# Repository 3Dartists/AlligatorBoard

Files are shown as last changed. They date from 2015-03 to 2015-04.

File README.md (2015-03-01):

Alligator Board
===============

The New Generation Electronic for RepRap 3D printer

The Alligator Board is designed to be a complete and reliable solution as RepRap 3D printer 
electronic control board. The base module features everything you need to build a standard 3D printer, 
and with the expansion piggy this is the most complete solution for complex 3D printer.

It is based on the 32 bit Cortex M3 ATSAM3X8EA-AU microcontroller (Arduino Due CPU)
This represents a big step forward towards greater computing power, compared to the existing 
solution based on 8 bit mcu. This means that this product is well suited for any kind of 3D printer, 
and is the ideal solution for Delta models, which require more complex calculus 
for its coordinates resolution. 

The professional design of every part takes care of the needs of the most exigent makers, 
ensuring best performances in your application. 

© 2014-2015 by Francesco Gargiulo. This work is made available under the Creative Commons 
Attribution-NonCommercial-ShareAlike 4.0 International License. [ CC-BY-NC-SA ]
To view a copy of this license, visit http://creativecommons.org/licenses/by-nc-sa/4.0/

This Designs ARE PROVIDED "AS IS WITH ALL FAULTS. The author disclaims all other warranties, express or implied.
The author is not responsible of any use of this design.
The author does not guarantee the correctness of the content of this repository (documents, schematics and gerber files), and offers no warranty or support for them. 
You may use these design files at your own risk, with no warranty about its behaviour. The author is not obliged to release updates every time that he introduces changes to the project.
The author may introduce changes to this designs and its specifications at any time, without notice. Also any other information about this product are subject to change without notice.
The project must not be intended as completed, but is continuously subject to be updated by the author. There is no guarantee that the documents in this repository are updated to the latest revision of the project.

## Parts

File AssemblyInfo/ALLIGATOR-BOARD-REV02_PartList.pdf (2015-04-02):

Description | Part Number | Manufacturer | Designator | Quantity
Capacitor 0603, 100nF X7R 25V | | | C1, C2_1, C2_2, C2_3, C3, C4, C6_1, C6_2, C6_3, C11_1, C11_2, C11_3, C14, C18, C24, C31, C33, C61_1, C61_2, C61_3, C61_4, C62_1, C62_2, C62_3, C62_4, C63_1, C63_2, C63_3, C63_4, C64, C65, C66, C67_1, C67_2, C70_1, C70_2, C72, C73, C75, C76, C79, C80, C89, C92, C93, C94, C95, C96, C97, C98, C100, C101, C102, C103, C104, C105, C107, C110, C112, C114, C115, C124, C127, C128_1, C128_2, C128_3, C128_4, C131, C133, C134, C136, C137, C138, C139, C140, C141 | 76
Capacitor 0603, 1nF X7R 50V | | | C5_1, C5_2, C5_3, C7_1, C7_2, C7_3, C10_1, C10_2, C10_3, C12_1, C12_2, C12_3, C32, C35, C36, C56, C154_1, C154_2 | 18
Capacitor 0805, 4.7uF X7R 16V | | | C9, C16, C17, C55, C69, C74, C91, C99, C106, C111, C130, C135, C153 | 13
Capacitor 1206, 1uF X7R 50V | | | C13_1, C13_2, C52, C90_1, C90_2 | 5
Capacitor 0603, 10pF NP0 50V | | | C15, C47, C48, C85, C86, C87, C88, C129 | 8
Capacitor 0603, 4.7pF C0G 50V | | | C19, C20, C21, C22, C23, C142, C143, C144, C145, C146 | 10
Capacitor 0603, 330pF X7R 50V | | | C25, C26, C37, C38, C45, C46, C117, C118, C119, C120, C121, C122, C123, C125, C132, C155 | 16
Aluminum Electrolytic Capacitors 100uF 50V | | | C27, C28, C29, C30, C39, C40, C41, C42, C49, C50, C126_1, C126_2, C126_3, C126_4 | 14
Capacitor 1206, 10uF X7R 16V | | | C43, C44 | 2
Capacitor 0603, 470nF X7R 25V | | | C51, C59_1, C59_2, C59_3, C59_4 | 5
Capacitor 0603, 22nF X7R 50V | | | C53 | 1
Capacitor 0603, 4.7nF X7R 50V | | | C54 | 1
Capacitor 0805, 100nF X7R 50V | | | C57_1, C57_2, C57_3, C57_4, C58_1, C58_2, C58_3, C58_4 | 8
Capacitor 0603, 10nF X7R 50V | | | C60_1, C60_2, C60_3, C60_4, C113, C116, C147 | 7
Capacitor 0603, 220nF X7R 25V | | | C68_1, C68_2 | 2
Capacitor 0805, 1uF X7R 16V | | | C71, C82 | 2
Capacitor 0603, 22pF NP0 50V | | | C77, C78, C108, C109, C148, C149 | 6
Capacitor 0603, 15pF NP0 50V | | | C81, C84 | 2
Capacitor 0603, 470pF X7R 50V | | | C83 | 1
Capacitor 1206, 4.7nnF X7R 630V | | | C150, C152 | 2
Capacitor 1210, 47nF 630V | | | C151 | 1
3.3Vdc HCMOS/TTL SMD CRYSTAL CLOCK OSCILLATOR 50MHz | ASV-50.000MHz-EJ | Abracon | CO1 | 1
Surface Mount 5V TRANSZORB Transient Voltage Suppressors | SMAJ5.0A | Vishay | D1, D13, D16, D30 | 4
High Speed switching diode | BAS516 | NXP | D2, D4, D17, D18, D19, D29 | 6
Double diode | BAV99 | NXP | D3_1, D3_2, D3_3, D5_1, D5_2, D5_3, D20_1, D20_2 | 8

## Alligator Board r02 - Partlist

60 V, 1 A ultra low VF MEGA Schottky barrier rectifiers | PMEG6010CEH,115 | NXP | D6_1, D6_2, D11 | 3
High-speed USB OTG ESD protection diode arrays | PUSBM5V5X4-TL,115 | NXP | D7 | 1
Surface Mount 33V TRANSZORB Transient Voltage Suppressors | SMBJ33A | Vishay | D8, D9, D10, D22 | 4
High-temperature 400 W Transient Voltage Suppressor | PTVS3V3S1UTR,115 | NXP | D14, D15, D26 | 3
Low capacitance TVS diode array | SR05.TCT | Semtech | D21 | 1
Low Capacitance Diode Array for ESD Protection in Four Data Lines | NUP4304MR6 | ON Semiconductor | D23, D24, D25, D27, D28 | 5
LED SMD 0603 Green | | | DL1_1, DL1_2, DL1_3, DL2_1, DL2_2, DL2_3, DL5, DL6_1, DL6_2 | 9
PolySwitch Resettable Devices- Ih=0.5A It=1.0A | MINISMDC050F-2 | TE CONNECTIVITY | F1 | 1
Generic 4 pin PCB Connector 3.81mm | | | J1_1, J1_2, J1_3 | 3
Micro-USB AB Receptacle, Right Angle, Top Mount, SMT, Lead-Free | 47590-0001 | Molex | J2, J7 | 2
Generic 2 pin PCB Connector 3.81mm | | | J3_1, J3_2, J10_1, J10_2 | 4
HEADER, 1.27MM, SMT, A 10 VIE | 20021121-00010C4LF | FCI | J4 | 1
Adimpex Generic 3 pin PCB Connector 3.81mm | | | J5 | 1
microSD Card Connector (Push-push Type) SCHA Series | SCHA5B0200 | ALPS | J6 | 1
4way Barrier Strip 8.26mm centerline | 4DB-P108-04 | TE Connectivity | J8 | 1
Generic 4 pin PCB Connector 5.08mm | | | J9_1, J9_2, J9_3, J9_4 | 4
RJ45 integrated magnetics connector SMD | J3011G21DNL | Pulse | J11 | 1
VERTICAL SMT RECEPTACLES 1.27mm 10x2 | | FCI | J12 | 1
2way Barrier Strip 8.26mm centerline | 4DB-P108-02 | TE Connectivity | J13_1, J13_2 | 2
2.54mm Pitch Surface Mount, Dual Row, Vertical, 10 Circuits | 15-91-0100 | Molex | J14 | 1
Unshrouded Header, SMT, Double Row, 26 Positions, 2.54 mm Pitch, Vertical | 95278-101-26LF | FCI | J15 | 1
VERTICAL SMT RECEPTACLES 1.27mm 8x2 | | FCI | J16 | 1
INDUCTOR 10UH 180MA 1210 10% Epcos B82422S1103K100 | B82422A1103K100 | Epcos | L1, L3 | 2
Ferrite Beads Chip - BLM21B Series | BLM21BD272SN1L | muRata | L2_1, L2_2, L2_3, L10, L14, L15 | 6
Noise Suppressor Trasnformer | | | L4, L16 | 2
Low Profile, High Current Inductors 1uH | | | L5, L7 | 2
Semi-shielded Power Inductors 10uH | SRN3015-100M | Bourns | L6, L11, L12 | 3
Semi-shielded Power Inductors 33uH | SRN8040-330M | Bourns | L9 | 1
N-Channel 40 V (D-S) MOSFET | Si2318CDS-T1-GE3 | Vishay | Q1_1, Q1_2 | 2
NPN General Pourpuse transistors | BC817 | NXP | Q2 | 1
OptiMOS 3 Power-Transistor | IPD036N04L G | Infineon | Q3_1, Q3_2 | 2
Single P-Channel, Logic Level PowerTrench MOSFET | FDN340P | Fairchild Semiconductor | Q4 | 1
Resistor 0603, 100 Kohm 1/10W - 1% | | | R1, R10_1, R10_2, R10_3, R18_1, R18_2, R18_3, R23, R24, R25, R44, R92, R102, R139 | 14
Resistor 0603, 1 Kohm 1/10W - 1% | | | R2, R6_1, R6_2, R6_3, R7_1, R7_2, R7_3, R14_1, R14_2, R14_3, R15_1, R15_2, R15_3, R63_1, R63_2 | 15

Resistor 0603, 10 Kohm 1/10W - 1% | R3, R5_1, R5_2, R5_3, R9_1, R9_2, R9_3, R13_1, R13_2, R13_3, R17_1, R17_2, R17_3, R20_1, R20_2, R21, R22, R36, R54, R55_1, R55_2, R55_3, R55_4, R56_1, R56_2, R56_3, R56_4, R59_1, R59_2, R59_3, R59_4, R60_1, R60_2, R60_3, R60_4, R61_1, R61_2, R61_3, R61_4, R62_1, R62_2, R62_3, R62_4, R67, R126_1, R126_2, R126_3, R126_4, R127_1, R127_2, R127_3, R127_4, R128_1, R128_2, R128_3, R128_4, R138_1, R138_2, R161, R162, R165, R171 | 62
Resistor 0603, 10 ohm 1/10W - 1% | R4_1, R4_2, R4_3, R12_1, R12_2, R12_3, R19_1, R19_2, R137_1, R137_2 | 10
Resistor 0603, 470 Kohm 1/10W - 1% | R8_1, R8_2, R8_3, R16_1, R16_2, R16_3 | 6
Resistor 0603, 4.7 Kohm 1/10W - 1% | R11, R64_1, R64_2, R82, R83, R84, R85, R86, R96, R98, R99, R100 | 12
Resistor 0603, 100 ohm 1/10W - 1% | R26, R27, R28, R29, R30, R31, R32, R37, R42, R48, R77, R87, R88, R89, R90, R93, R94, R107, R163 | 19
Resistor 0603, 39 ohm 1/10W - 1% | R33, R34 | 2
Resistor 0603, 6K8 Kohm 1/10W - 1% | R35 | 1
Resistor 0603, 22 ohm 1/10W - 1% | R38, R39, R40, R41, R43, R66_1, R66_2, R71, R72, R125_1, R125_2, R125_3, R125_4, R154, R155, R156_1, R156_2, R156_3, R156_4, R157_1, R157_2, R157_3, R157_4, R158_1, R158_2, R158_3, R158_4 | 27
Resistor 0603, 47 ohm 1/10W - 1% | R45, R75, R76, R104, R105, R106, R108, R109, R110, R111, R112, R113, R114, R115, R116, R117, R118, R119, R120, R121, R122, R123, R124, R129, R130, R131, R132, R133, R134, R135, R140, R141, R142, R143, R144, R145, R146, R147, R148, R149, R150, R151, R152, R153, R164, R166, R167, R168, R169, R174, R175, R176 | 52
Resistor 0603, 47 Kohm 1/10W - 1% | R46 | 1
Resistor 0603, 0 ohm 1/10W - 1% | R47, R97, R103, R170 | 4
Resistor 0603, 330 ohm 1/10W - 1% | R49_1, R49_2, R91, R95 | 4
Resistor 0603, 220 ohm 1/10W - 1% | R50 | 1
Resistor 0603, 56.2 Kohm 1/10W - 1% | R51 | 1
Resistor 0603, 0.68 ohm 1/10W - 1% | R52 | 1
Resistor 0603, 1 Mohm 1/10W - 1% | R53_1, R53_2, R53_3, R53_4 | 4
Power Resistor - 0.2 ohm 1% - 2512 | R57_1, R57_2, R57_3, R57_4, R58_1, R58_2, R58_3, R58_4 | 8
Resistor 0603, 12 Kohm 1/10W - 1% | R68 | 1
Resistor 0603, 4.42 Kohm 1/10W - 1% | R69, R70 | 2
Resistor 0603, 8.2 Kohm 1/10W - 1% | R73_1, R73_2 | 2
Resistor 0603, 15 Kohm 1/10W - 1% | R74_1, R74_2 | 2
Resistor 0603, 49.9 ohm 1/10W - 1% | R78, R79, R80, R81 | 4
Resistor 0603, 12.1 Kohm 1/10W - 1% | R101 | 1

Resistor 0805, 1 Kohm 1/8W - 1% | R136_1, R136_2 | 2
SPDT SLIDE SWITCH | | | S3_1, S3_2 | 2
SPDT SLIDE SWITCH | | | S4 | 1
ACM7060 Common Mode Filter for power line | ACM7060-701-2PL-TL01 | TDK | T1 | 1
Low Offset Voltage Dual Comparator | LM393DMR2G | On Semiconductor | U1_1, U1_2, U1_3 | 3
AT91SAM ARM Cortex M3 Flash MCU | ATSAM3X8EA-AU | Atmel | U2 | 1
8-Bit Micro Power QUAD Digital-to-Analog Converter with Rail-to-Rail Output | DAC084S085CIMM/NOPB | Texas Instrument | U3 | 1
1.0 A 3,3V - Low-Dropout Positive Fixed Voltage Regulator | NCP1117DT33G | On Semiconductor | U5 | 1
42V, 1.0A Step-Down Switching Regulator | LM25010MHX/NOPB | Texas Instrument | U6 | 1
STEPPER MOTOR CONTROLLER IC | DRV8825PWP | Texas Instrument | U7_1, U7_2, U7_3, U7_4 | 4
64K SPI Bus Serial EEPROM | 25AA640A-I/MS | Microchip | U8 | 1
2K SPI Bus Serial EEPROM with EUI-48 Node Identity | 25AA02E48T-I/OT | Microchip | U9 | 1
32 Mbit SPI Serial Flash | SST25VF032B-80-4I-S2AF | SST | U10 | 1
Low-Offset, Rail-to-Rail I/O Operational Amplifier | OPA2317ID | Texas Instrument | U12_1, U12_2 | 2
3.3V Single Power Supply, 10/100 Physical Layer Transceiver | LAN8720Ai-CP | SMSC | U13 | 1
NPN/PNP transistor pair connected as push-pull driver | PMD2001D,115 | NXP | U14_1, U14_2 | 2
Single Channel Hi-Speed USB to multipurpose UART/FIFO IC | FT232HL | FTDI | U15 | 1
Dual 4-channel analog multiplexer/demultiplexer | CD4052BPWR | Texas Instrument | U16 | 1
12MHz ULTRA MINIATURE CERAMIC GLASS SEALED SMD CRYSTAL | ABM8G-12.000MHZ-18-D2Y-T | Abracon | Y1, Y2 | 2

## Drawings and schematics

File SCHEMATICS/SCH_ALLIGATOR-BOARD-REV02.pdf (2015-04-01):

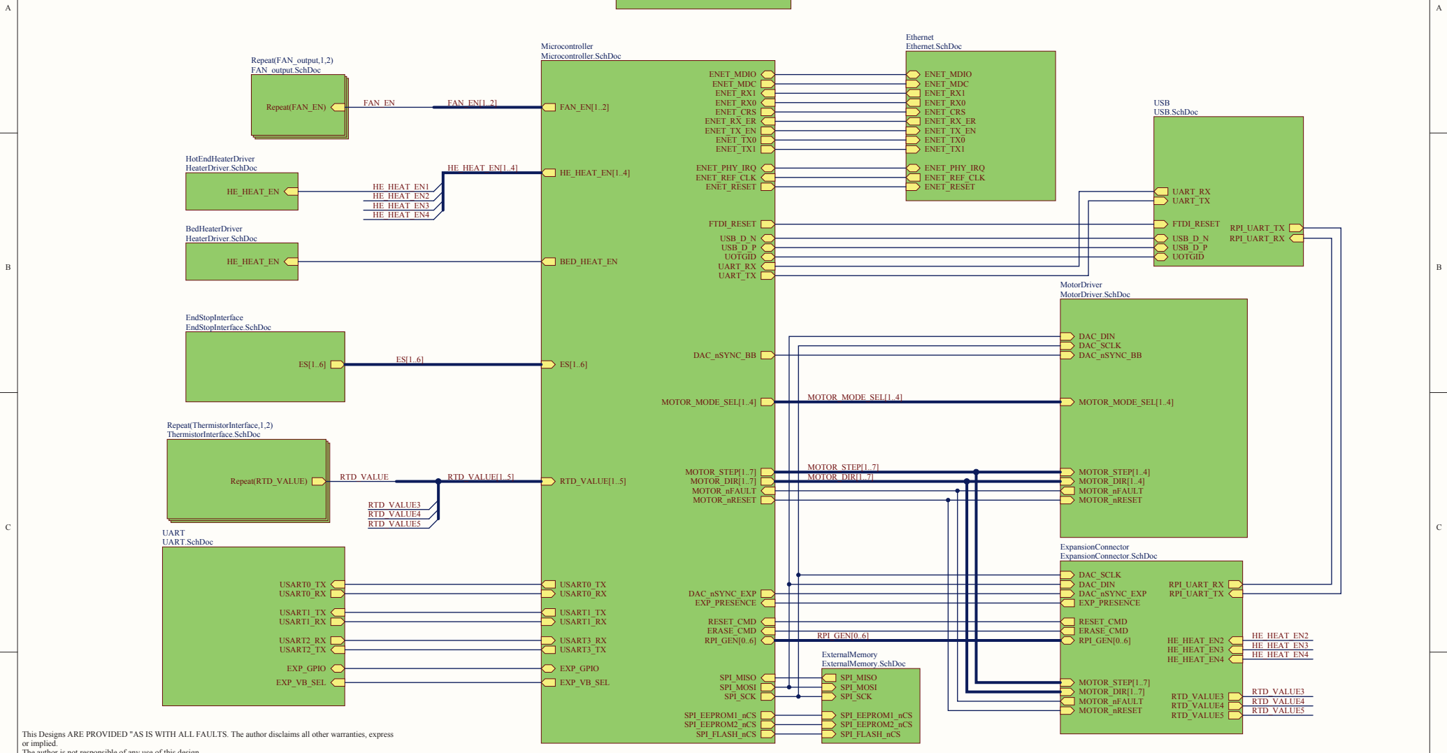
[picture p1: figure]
or implied.; ENET_MDIO ENET_MDC ENET_RX1 ENET_RX0 ENET_CRS; ENET_TX_EN ENET_TX0 ENET_TX1; ENET_REF_CLK; ENET_RX_ER; ENET_PHY_IRQ; MOTOR_DIR[1..7]; DAC_nSYNC_BB; DAC_nSYNC_EXP; MOTOR_STEP[1..7]; FAN_EN[1..2]; HE_HEAT_EN[1..4]; BED_HEAT_EN; RTD_VALUE[1..5]; USART0_RX; USART0_TX; USART1_RX; USART1_TX; UART_RX UART_TX; MOTOR_nFAULT; SPI_EEPROM1_nCS; SPI_MISO SPI_MOSI SPI_SCK; SPI_EEPROM2_nCS SPI_FLASH_nCS; ENET_RESET; MOTOR_nRESET; USB_D_N USB_D_P UOTGID; FTDI_RESET; USART3_RX; RPI_GEN[0..6]; USART3_TX; EXP_PRESENCE; ERASE_CMD; MOTOR_MODE_SEL[1..4]; RESET_CMD; EXP_GPIO; EXP_VB_SEL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

D | D

Designed by:; Checked by:; Verified by:; Rev.:; TITLE; PROJECT; F.Gargiulo; R.Capponi; M.Antonini; Alligator Board - 3D Printer Electronic; TOPSHEET

3D Artists - http://www.3dartists.org | Sheet: | of:
ALLIGATOR-BOARD | Configuration Variant 0 © Francesco Gargiulo, 2015

© 2015 by Francesco Gargiulo. This work is made available under the Creative Commons Attribution-NonCommercial-ShareAlike 4.0 International License. To view a copy of this license, visit http://creativecommons.org/licenses/by-nc-sa/4.0/

This Designs ARE PROVIDED "AS IS WITH ALL FAULTS. The author disclaims all other warranties, express

The author is not responsible of any use of this design.
The author does not guarantee the correctness of these documents, and offers no warranty or support for them. You may use these design files at your own risk, with no warranty about its behaviour.
The author may introduce changes to this designs and its specifications at any time, without notice. Also any other information about this product are subject to change without notice.
The project must not be intended as completed, but is continuously subject to be updated by the author. There is no guarantee that this document is updated to the latest revision of the project.

PowerSupply
PowerSupply.SchDoc

# The new generation electronic for 3D printers

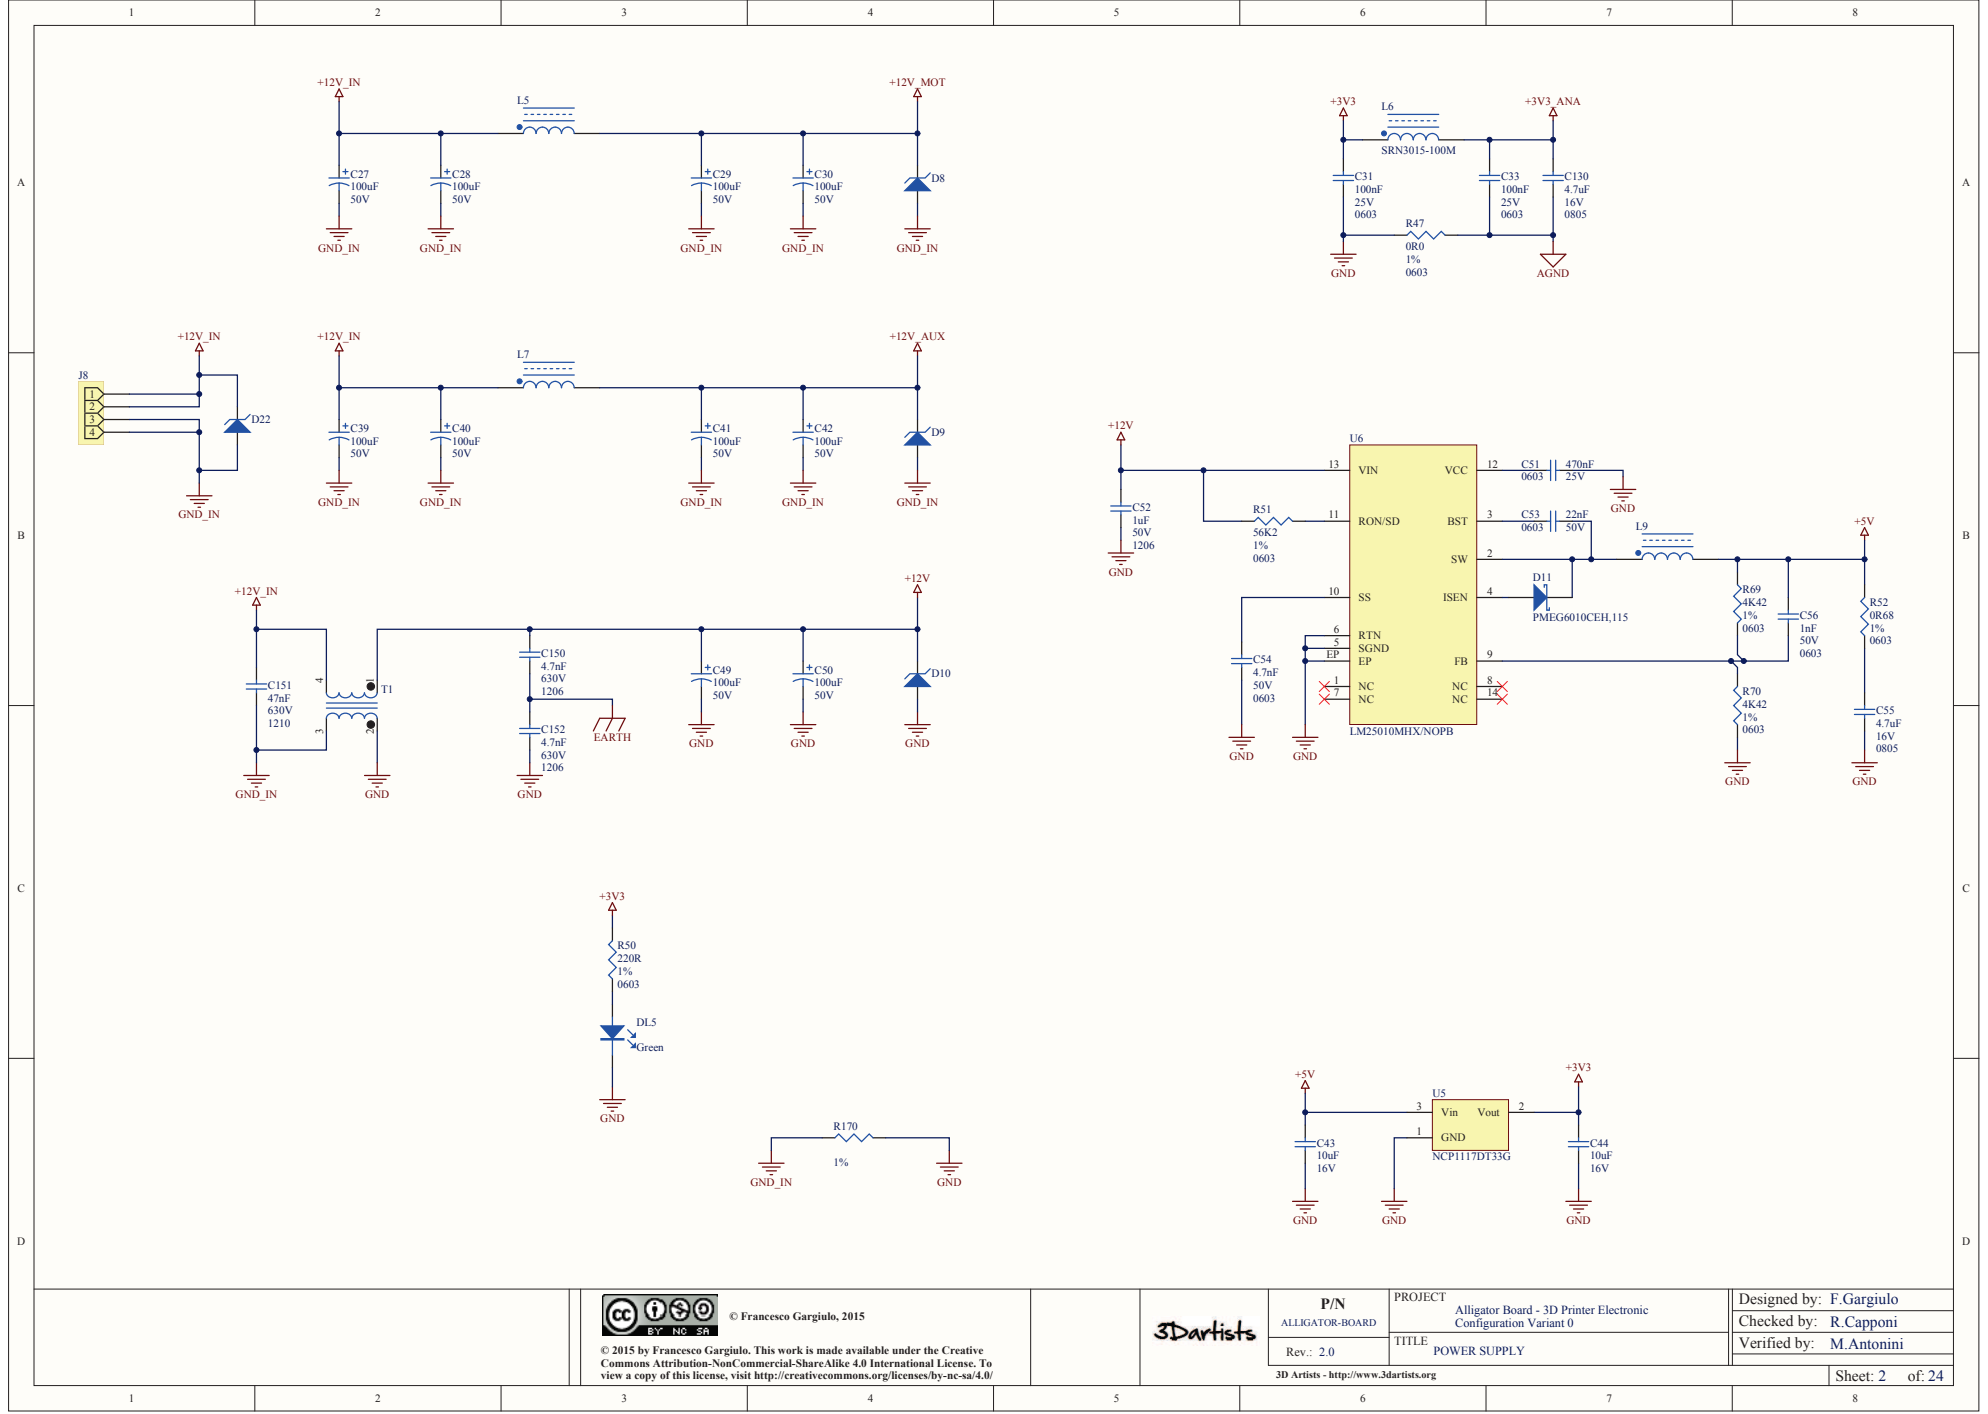
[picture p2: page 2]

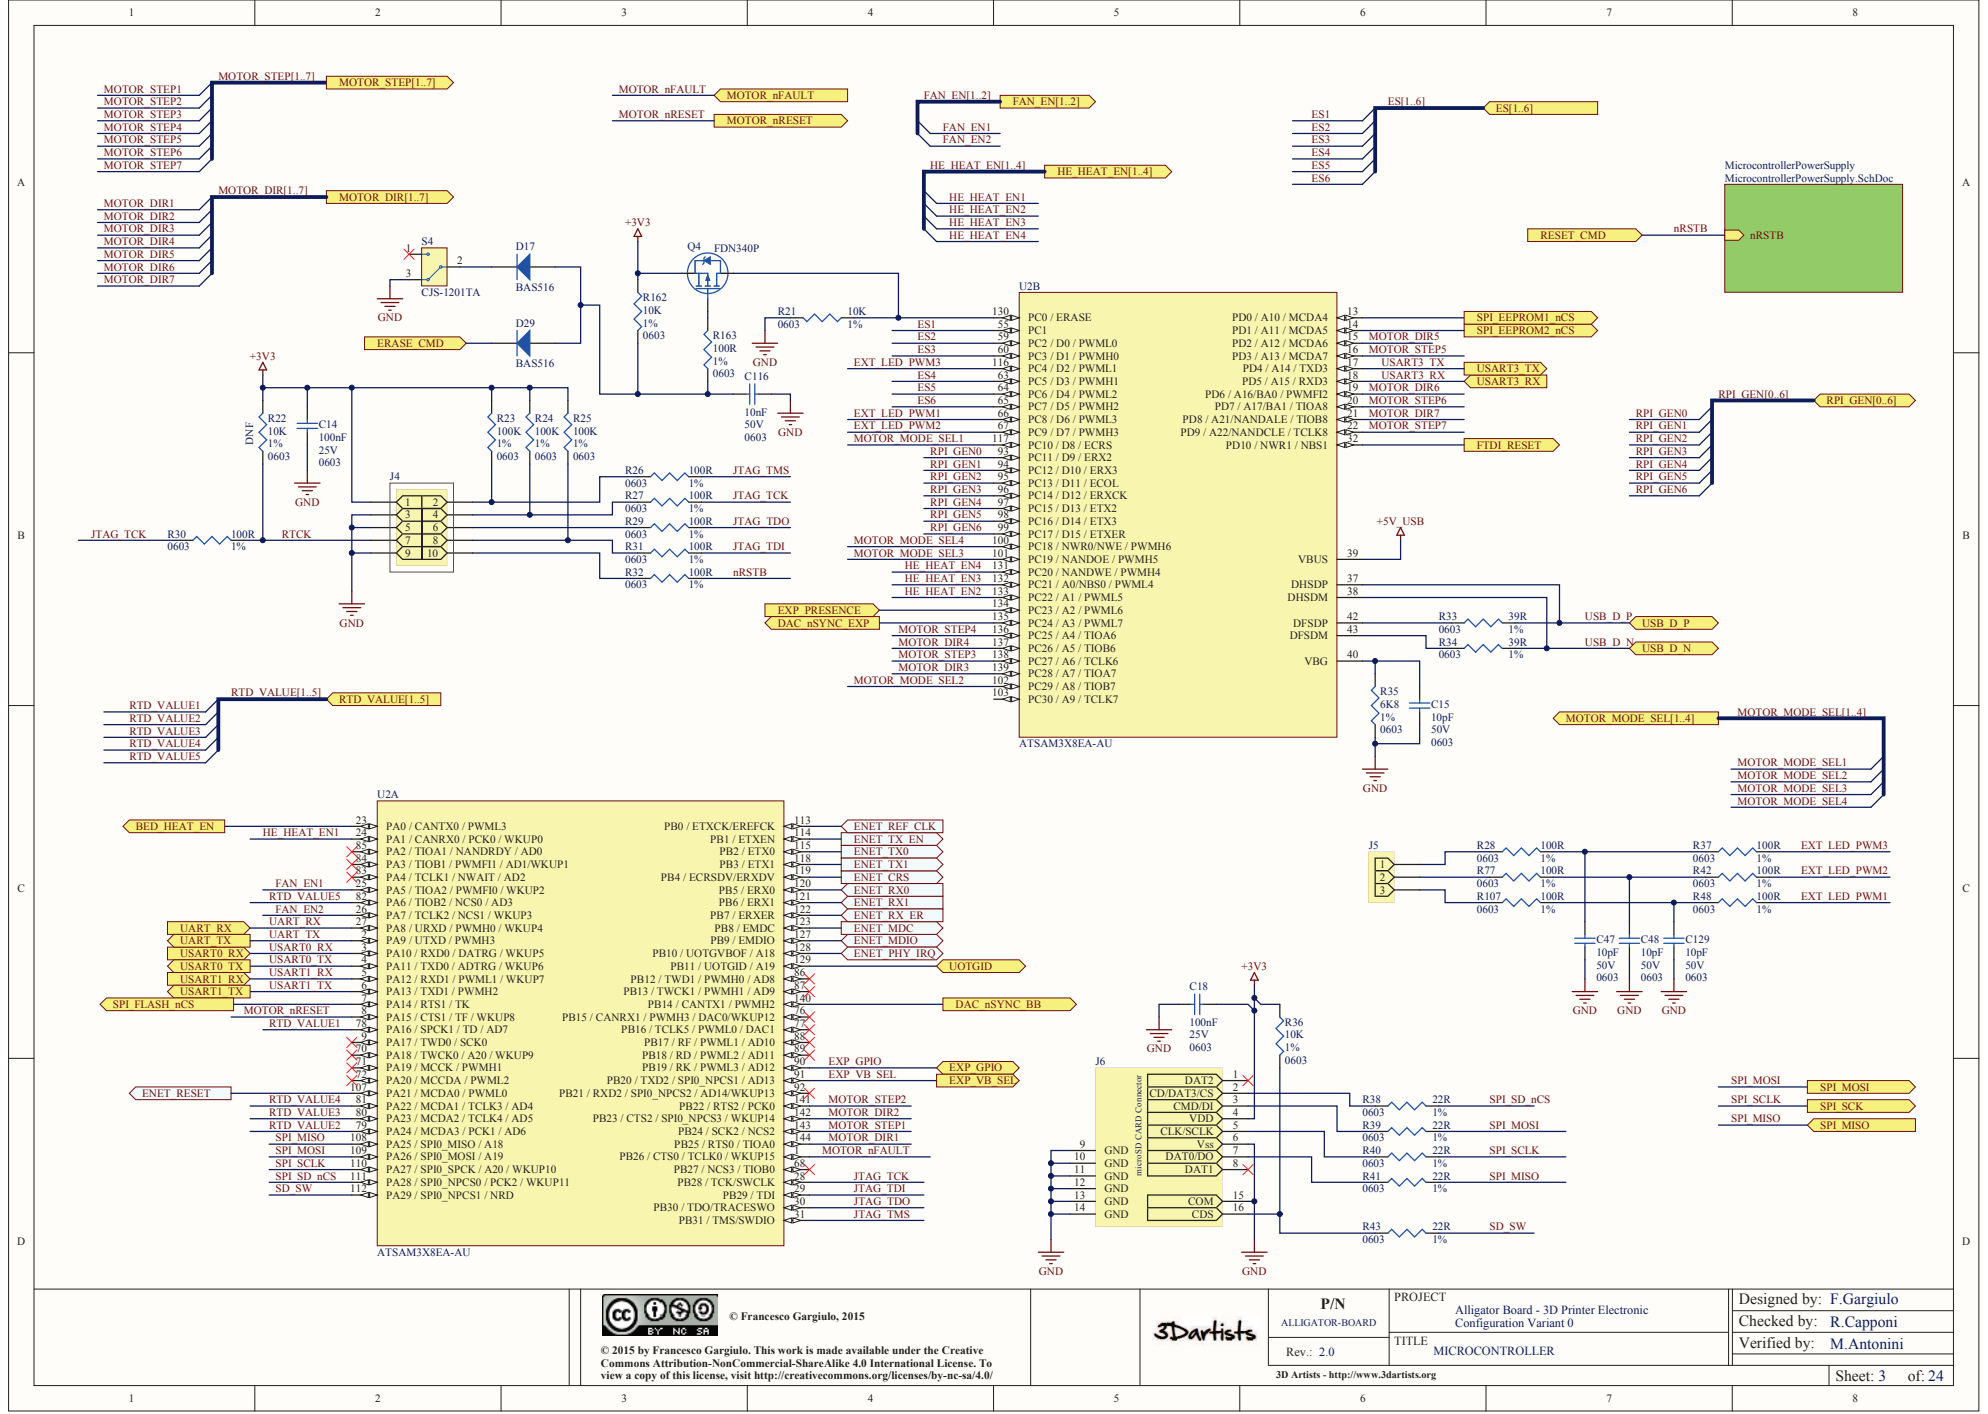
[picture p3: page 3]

microSD CARD Connector CLK/SCLK
CD/DAT3/CS
CMD/DI
VDD
CLK/SCLK

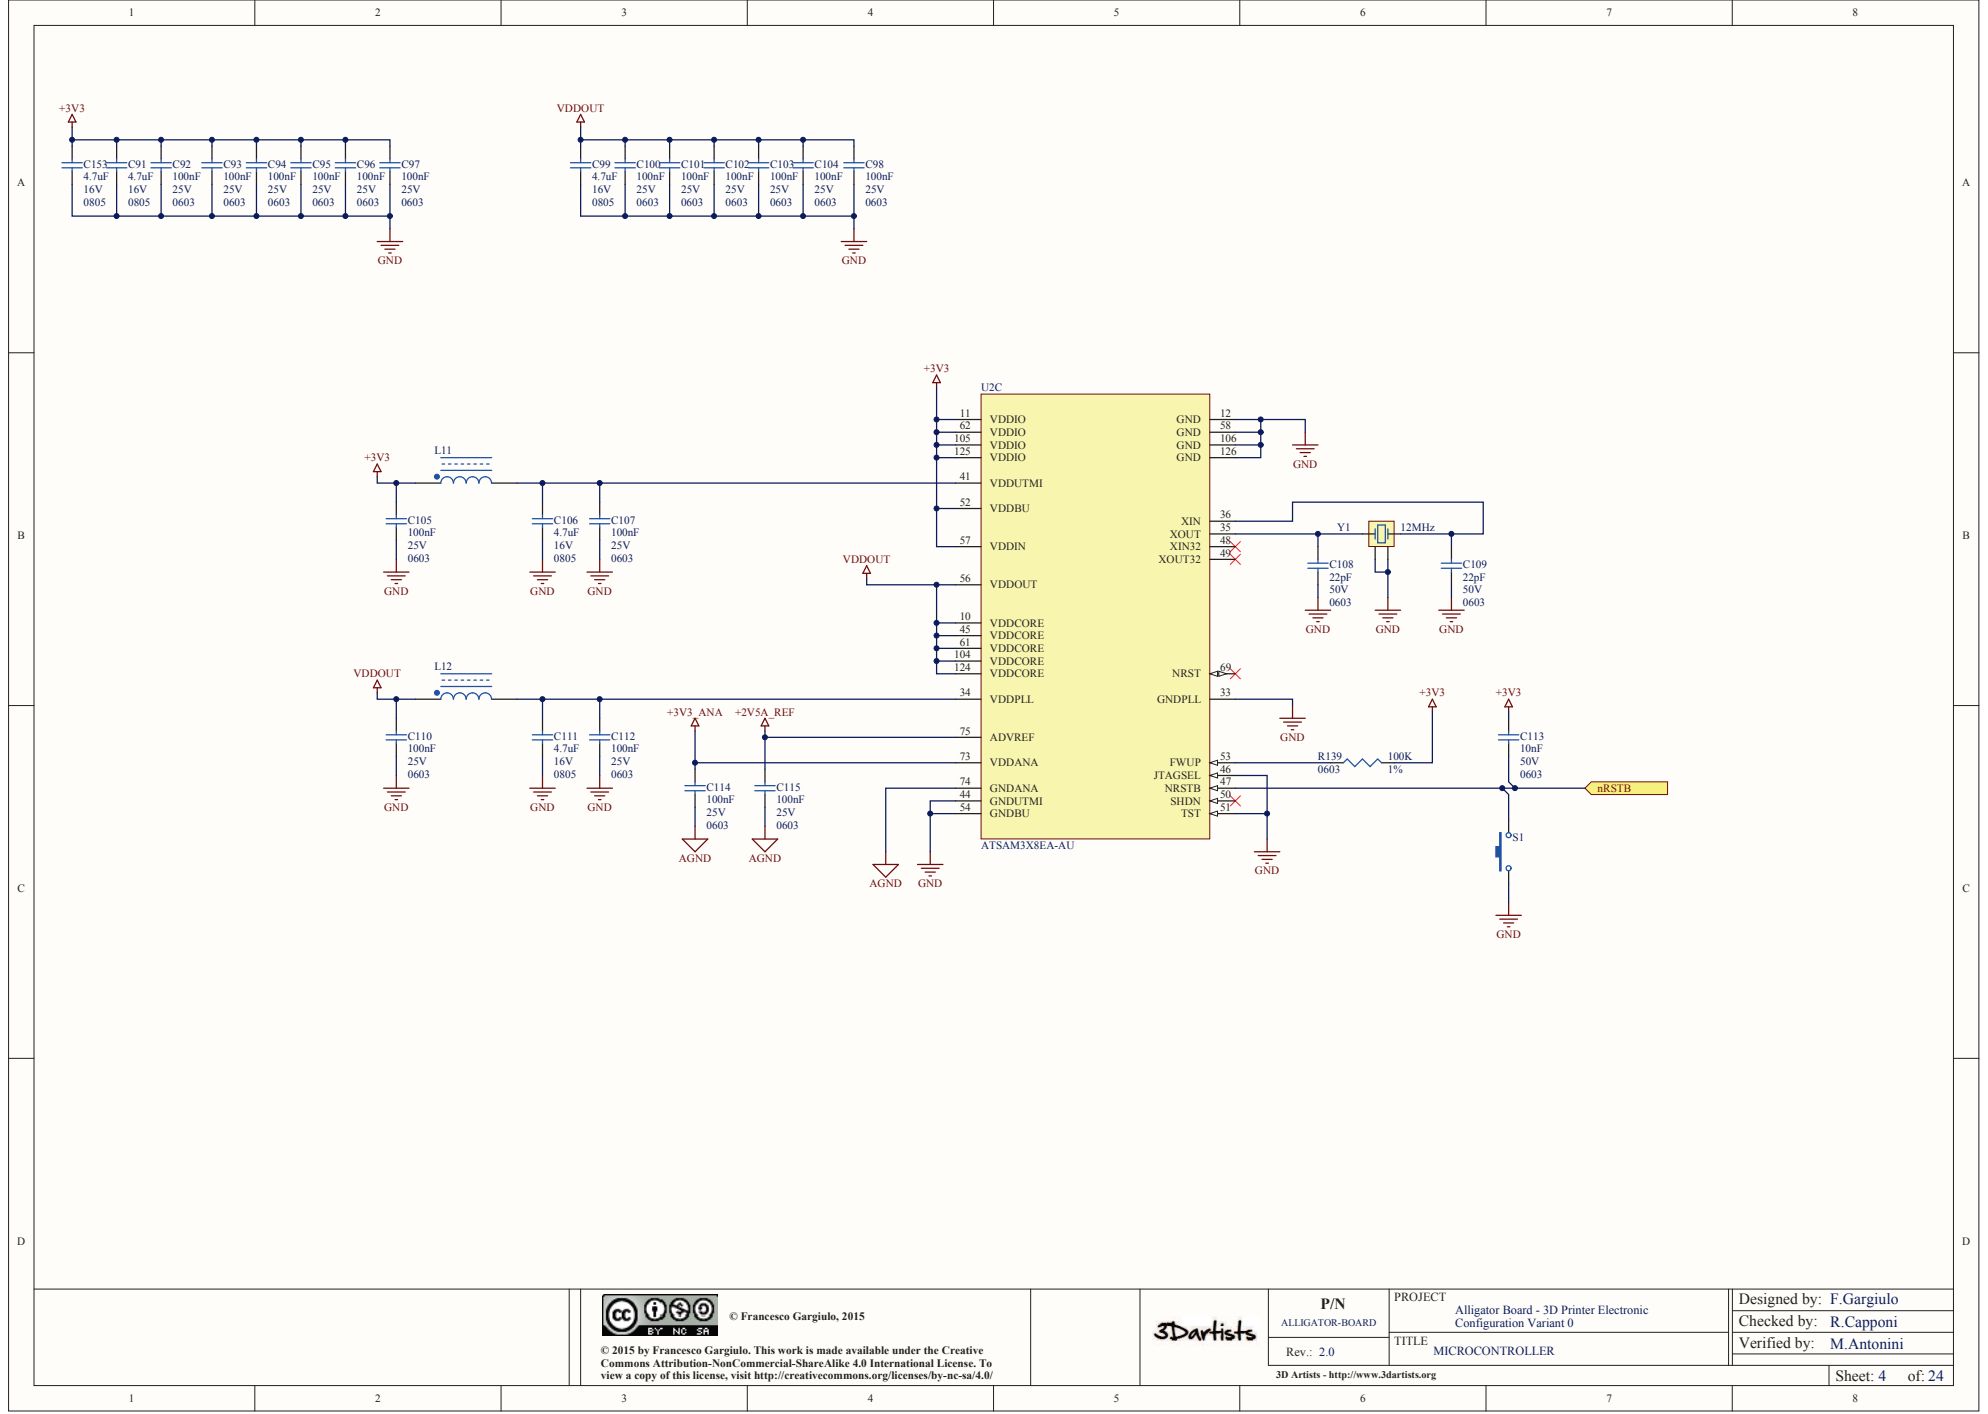
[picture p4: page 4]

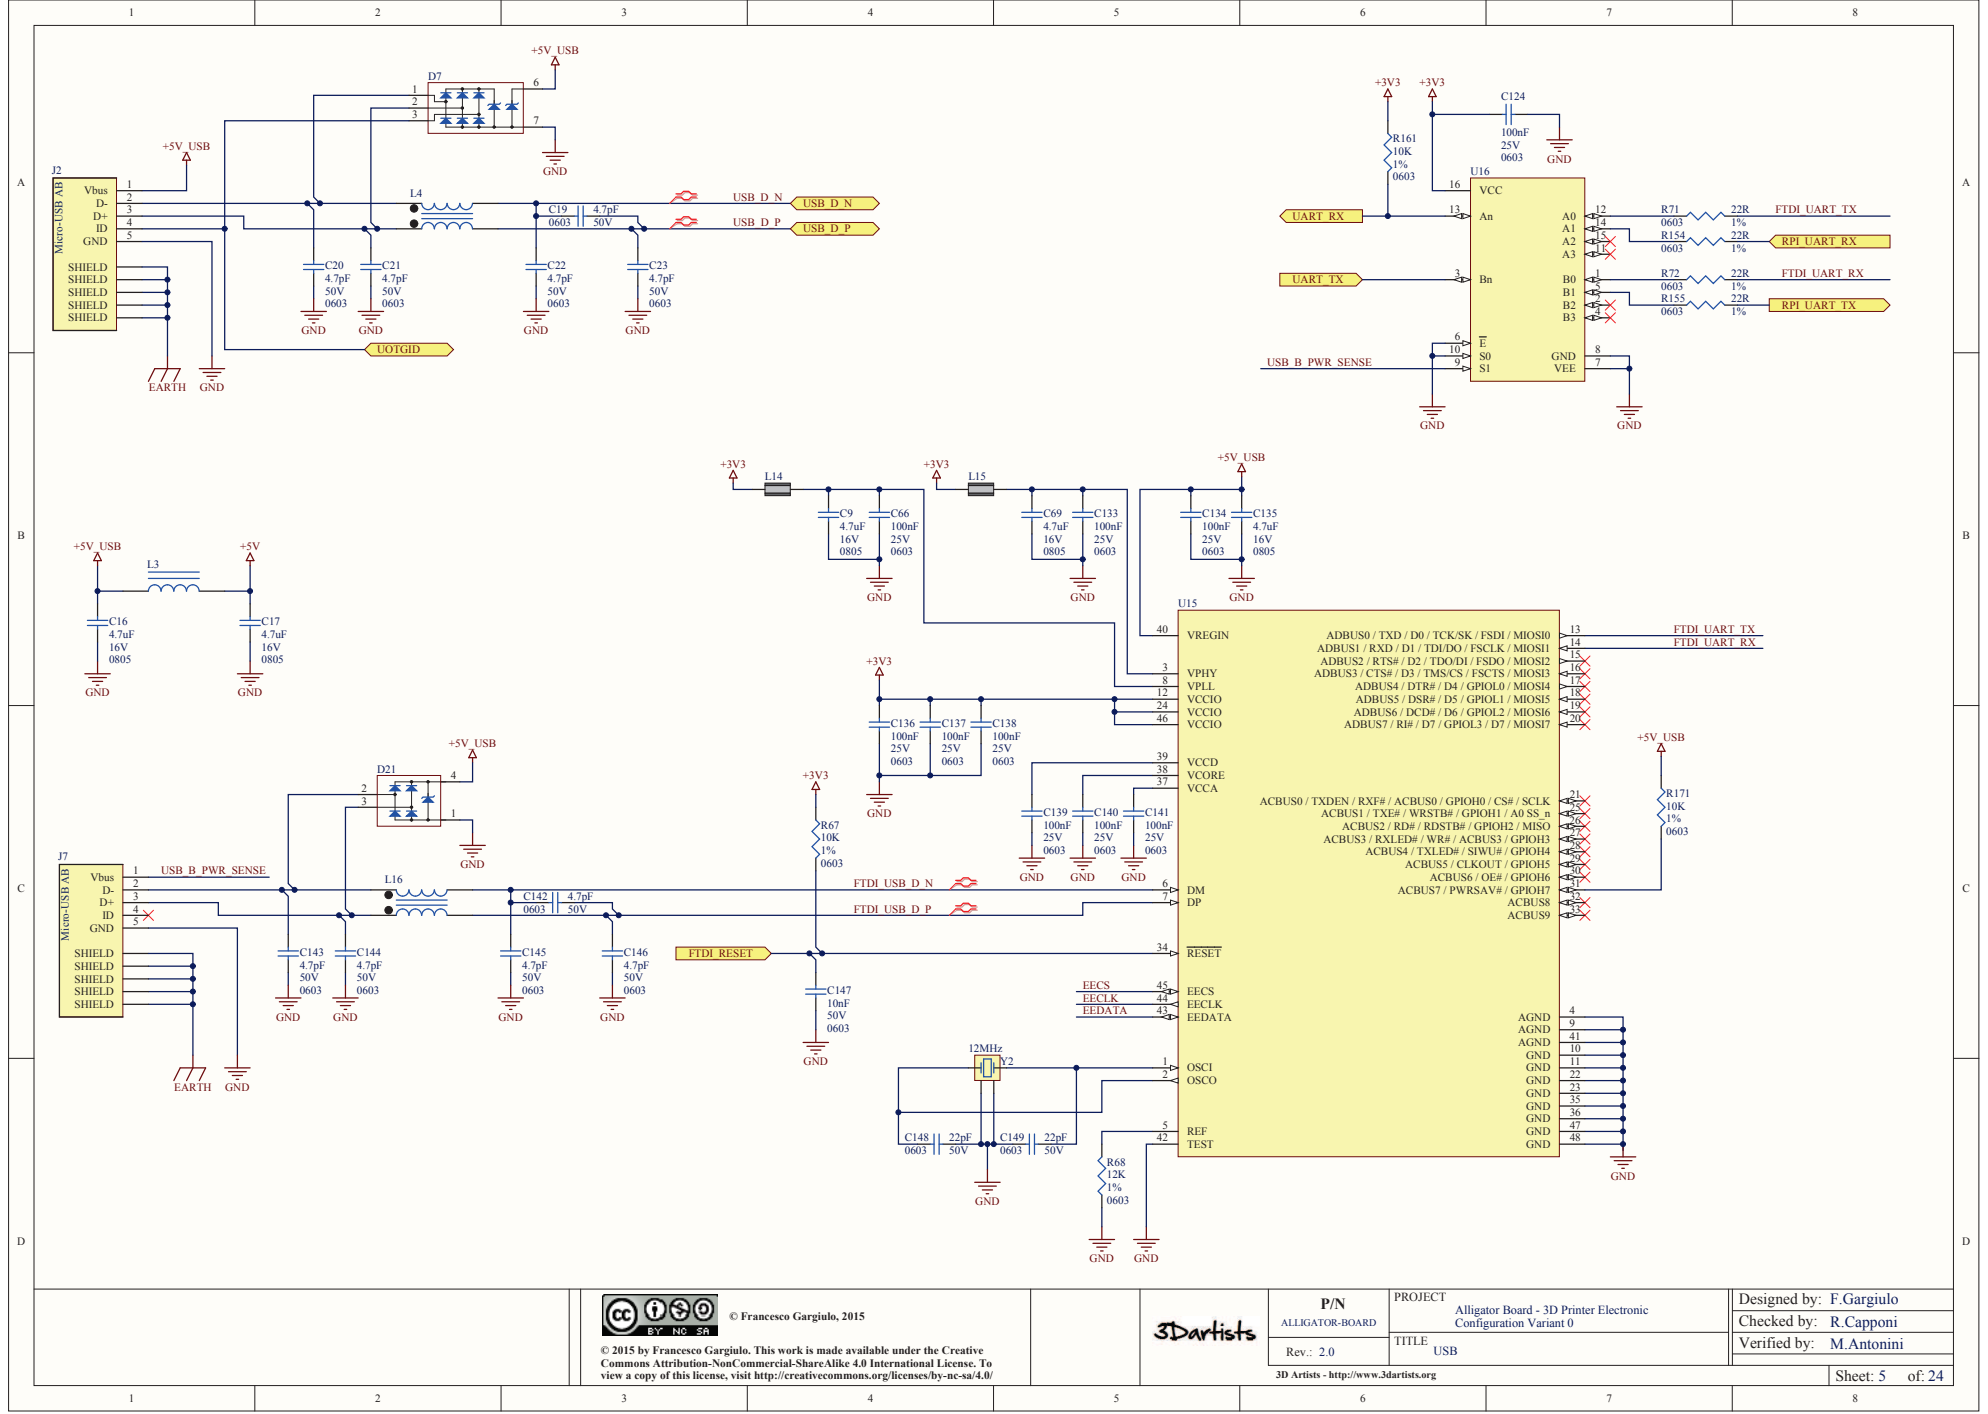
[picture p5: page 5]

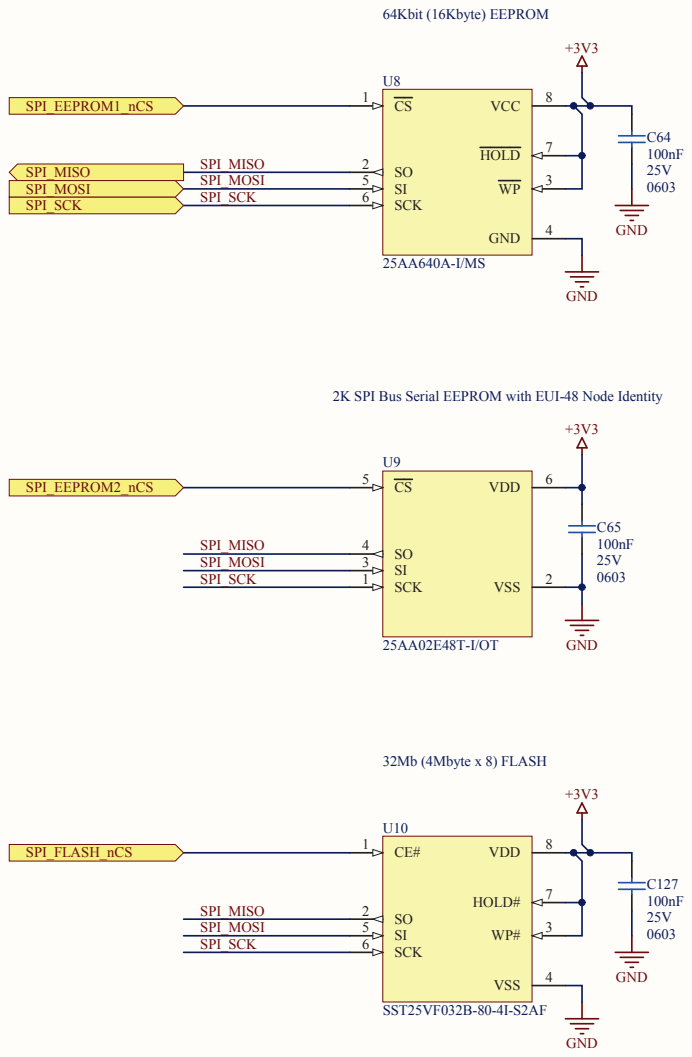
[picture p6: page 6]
EXTERNAL MEMORY; SPI_MOSI; 32Mb (4Mbyte x 8) FLASH; GND; SPI_MISO; SPI_SCK; SPI_EEPROM2_nCS; SPI_FLASH_nCS; SCK 1; VSS; VDD; SCK 6; HOLD#; SST25VF032B-80-4I-S2AF; SPI_EEPROM1_nCS; SPI_MISO SPI_MOSI SPI_SCK; HOLD; VCC; 64Kbit (16Kbyte) EEPROM

2K SPI Bus Serial EEPROM with EUI-48 Node Identity

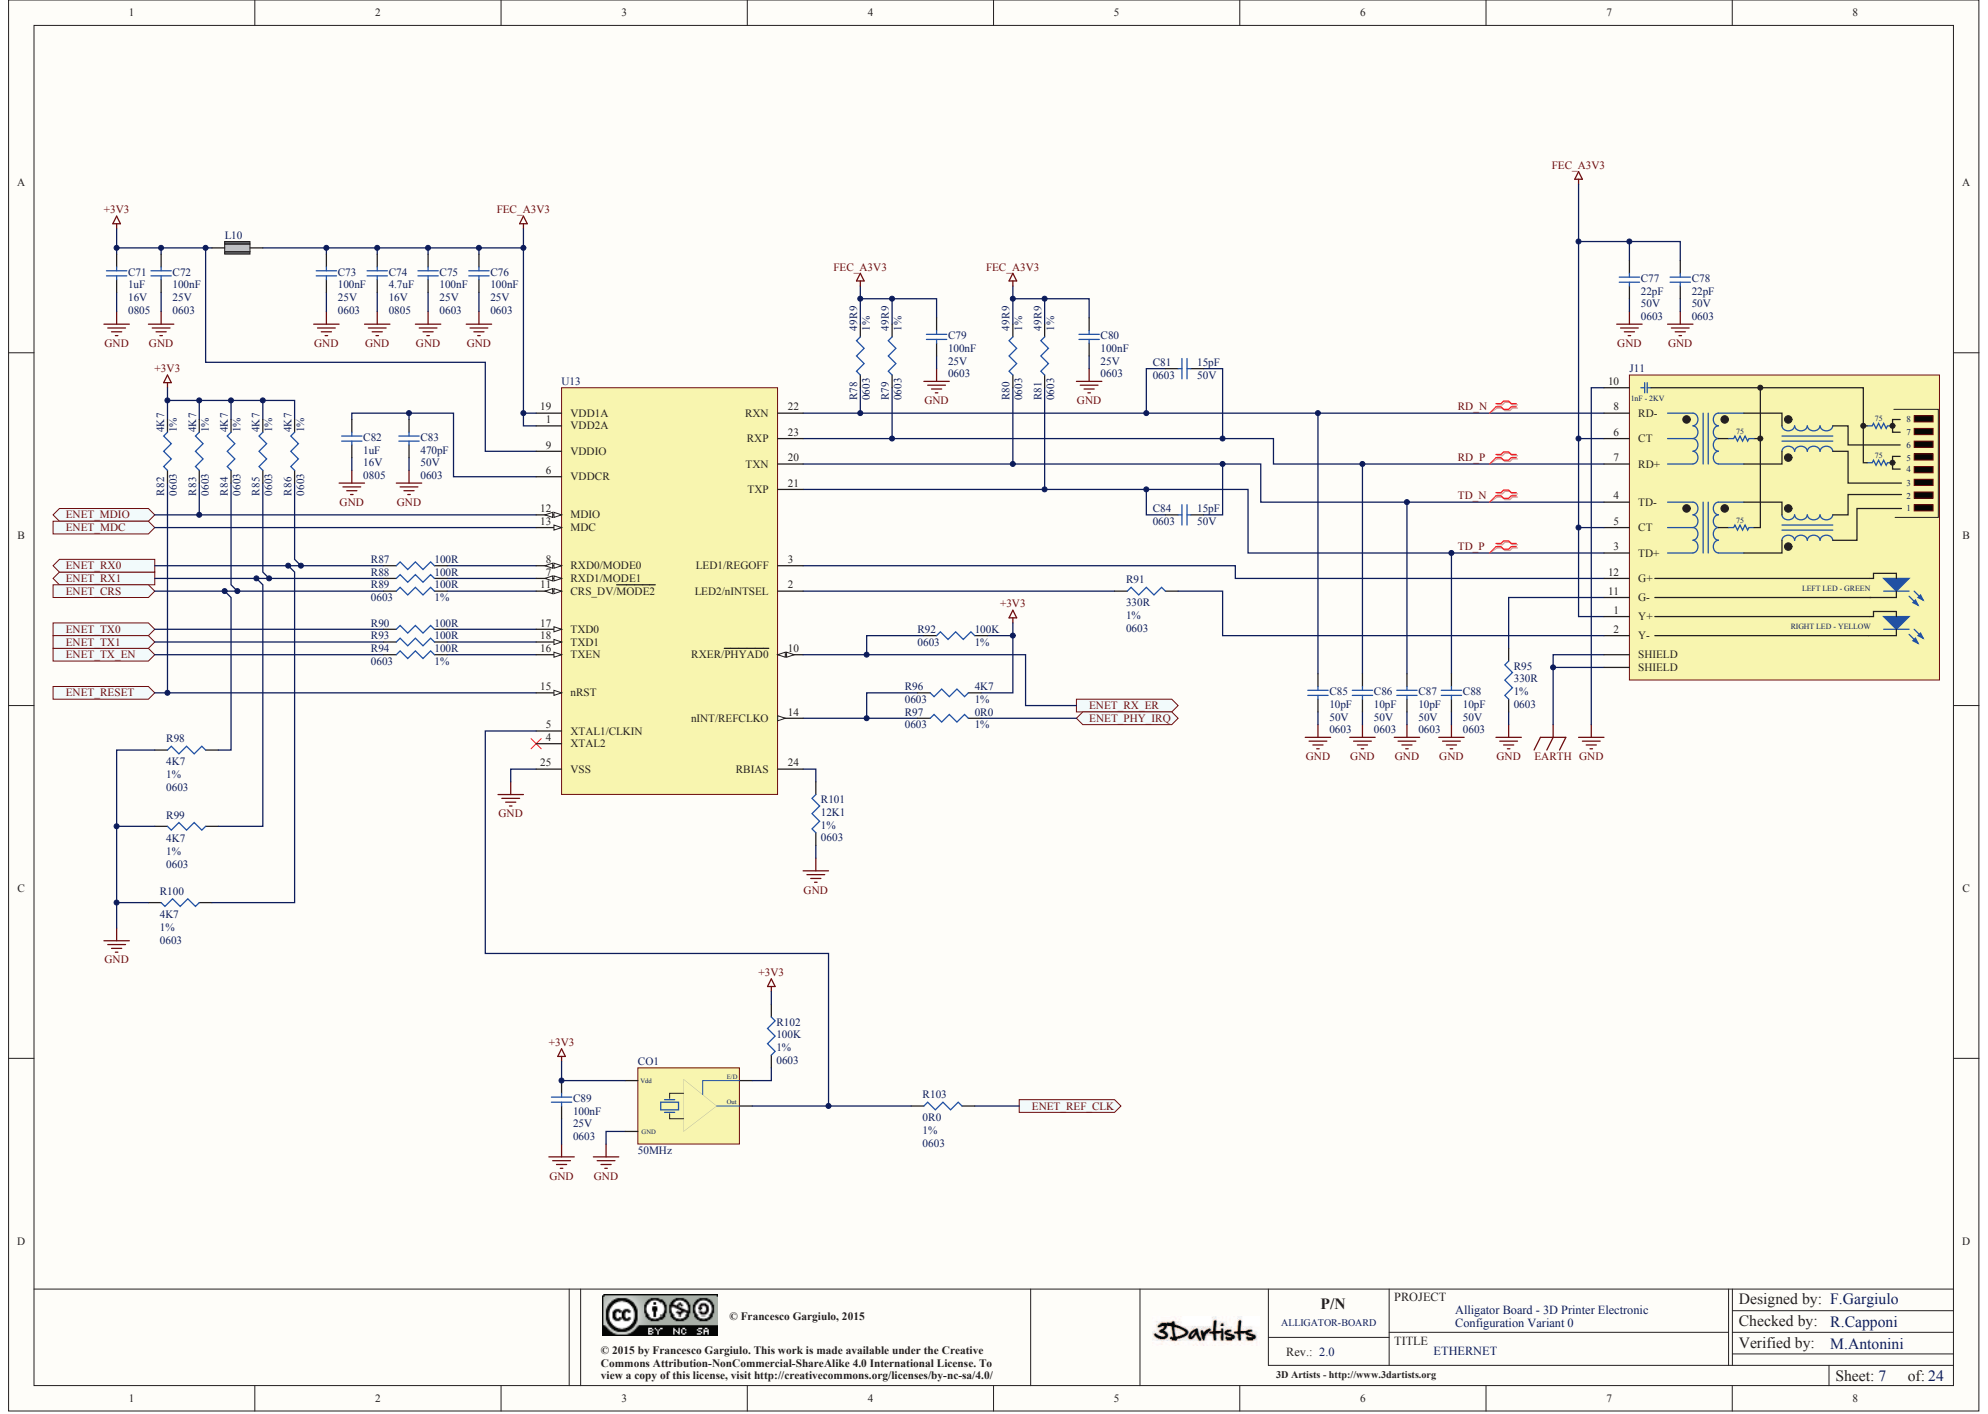
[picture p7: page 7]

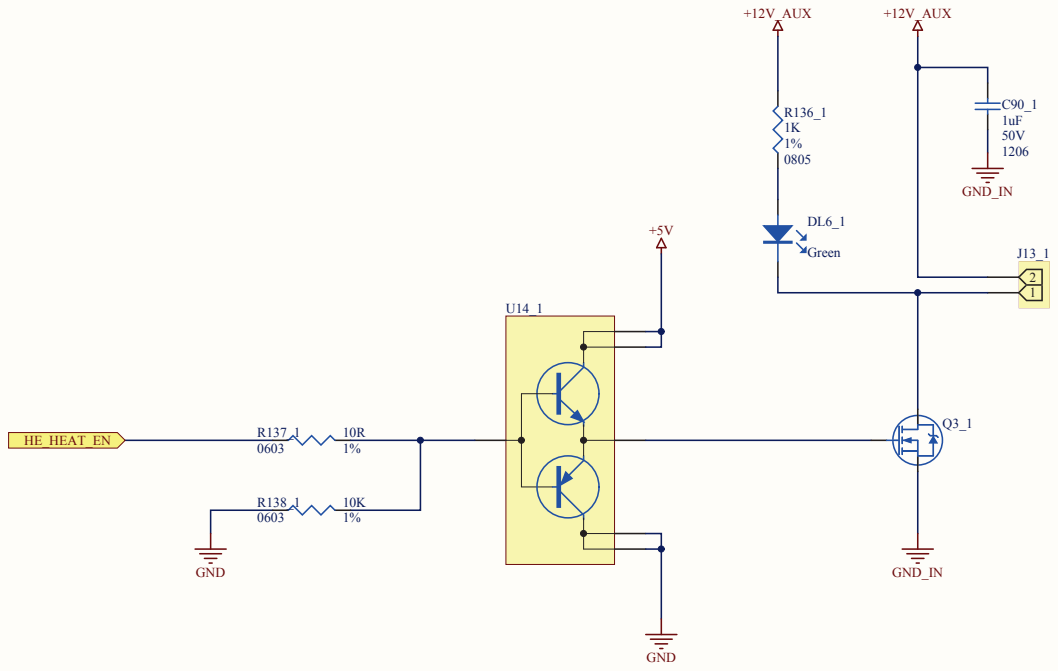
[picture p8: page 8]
HE_HEAT_EN; +12V_AUX; Green; GND_IN; GND

HOT-END HEATER DRIVER

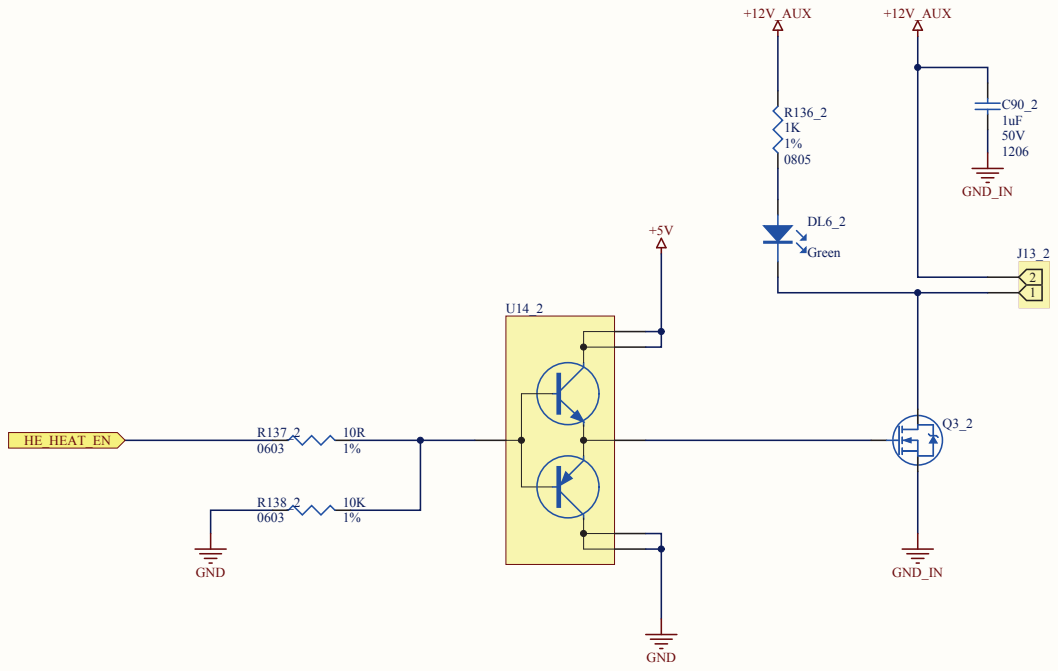
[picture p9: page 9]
HE_HEAT_EN; +12V_AUX; Green; GND_IN; GND

HOT-END HEATER DRIVER

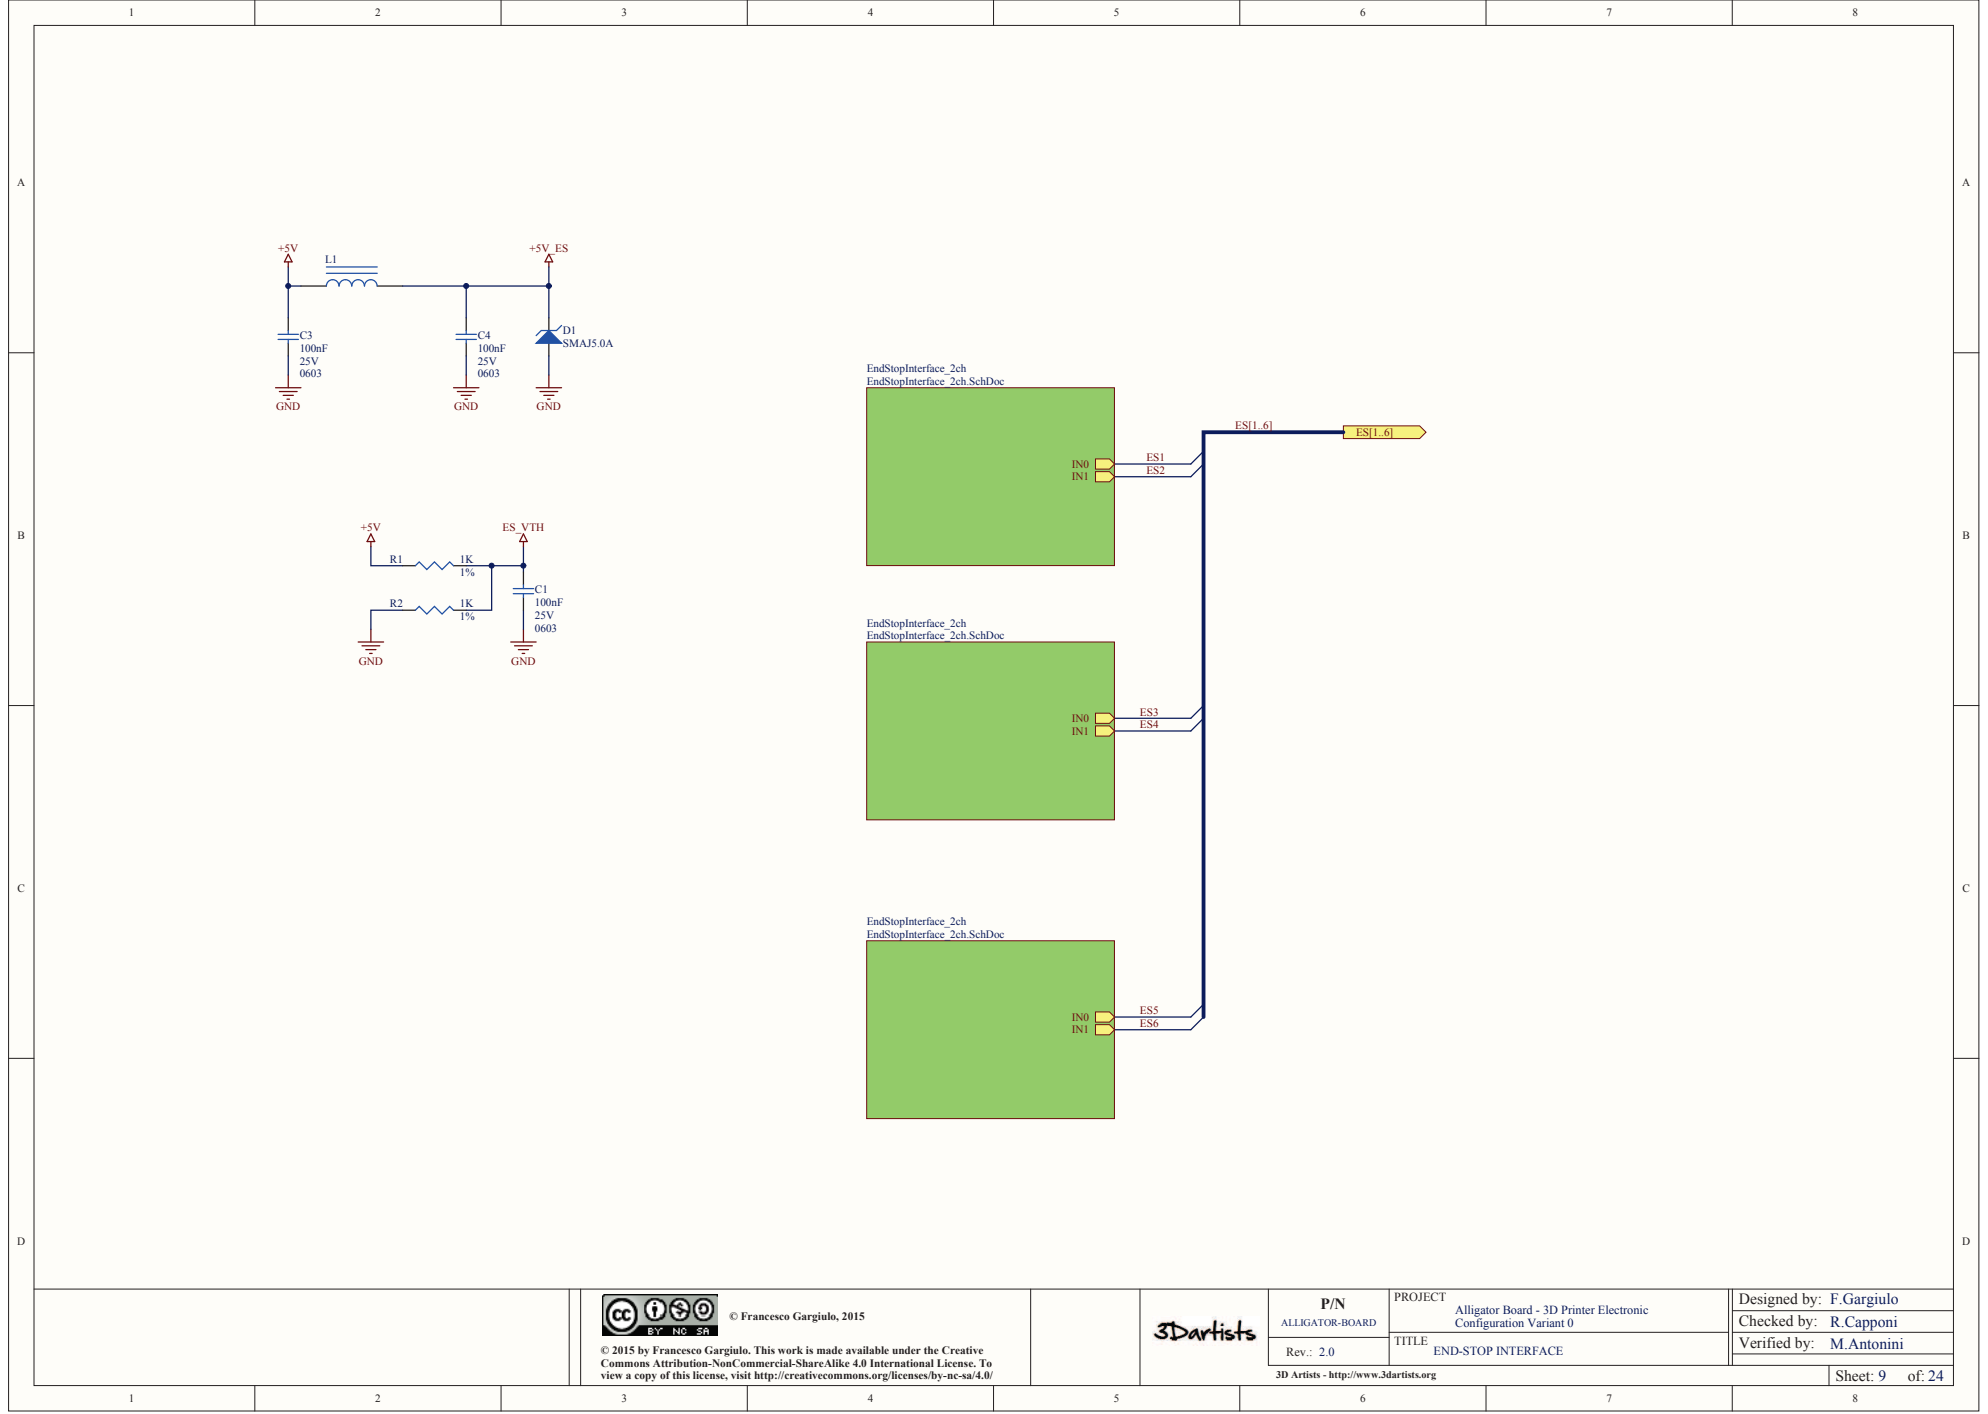
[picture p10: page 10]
GND; ES_VTH; EndStopInterface_2ch EndStopInterface_2ch.SchDoc; D1 SMAJ5.0A

END-STOP INTERFACE

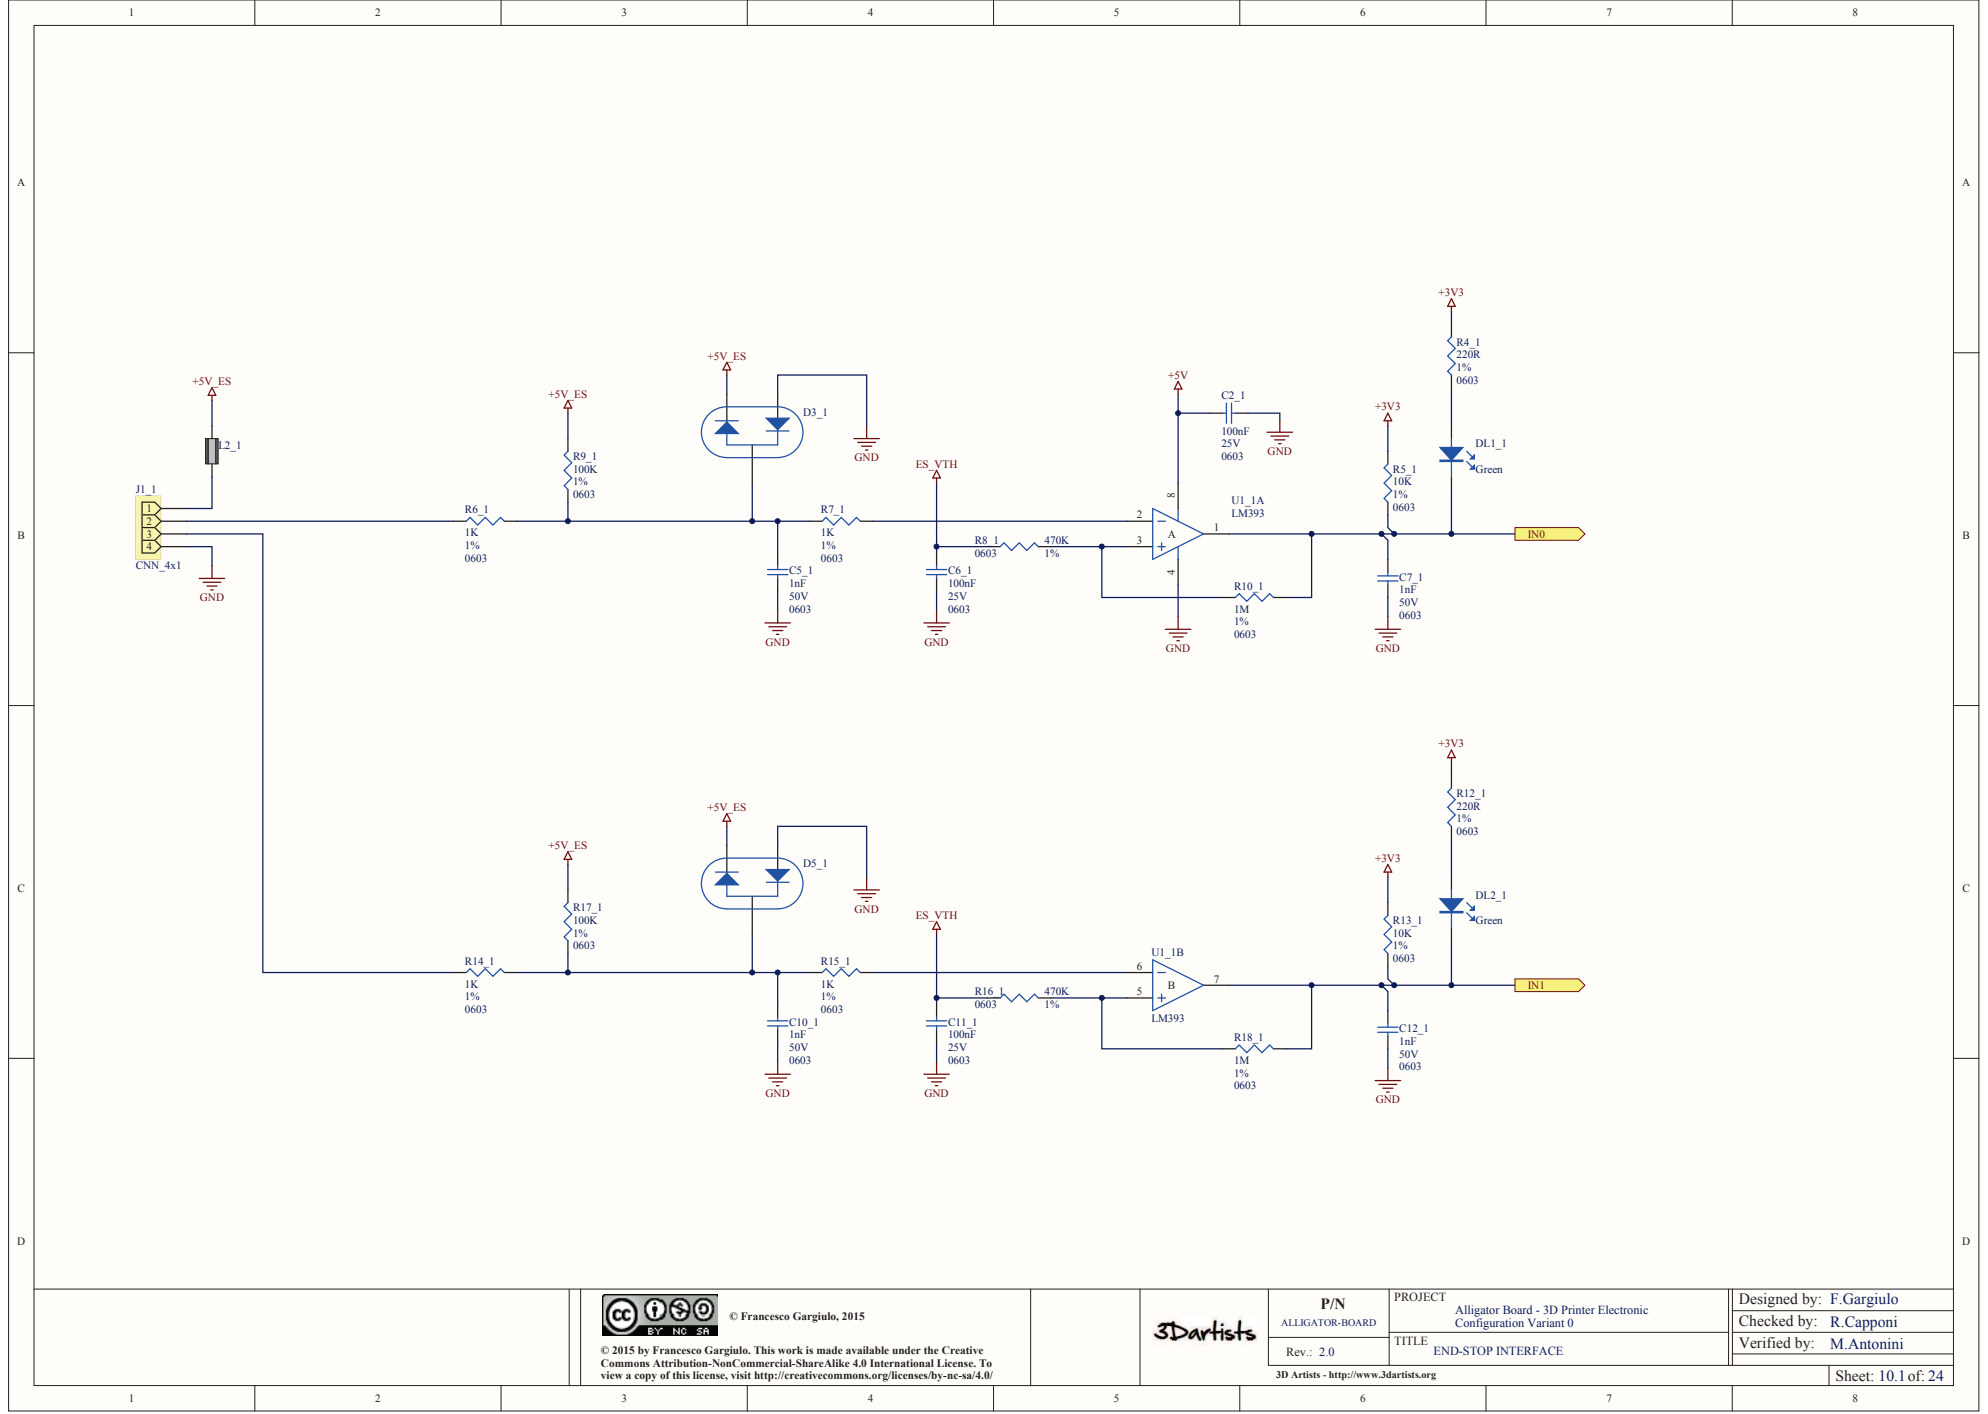
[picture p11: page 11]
GND; ES_VTH; Green; CNN_4x1

END-STOP INTERFACE

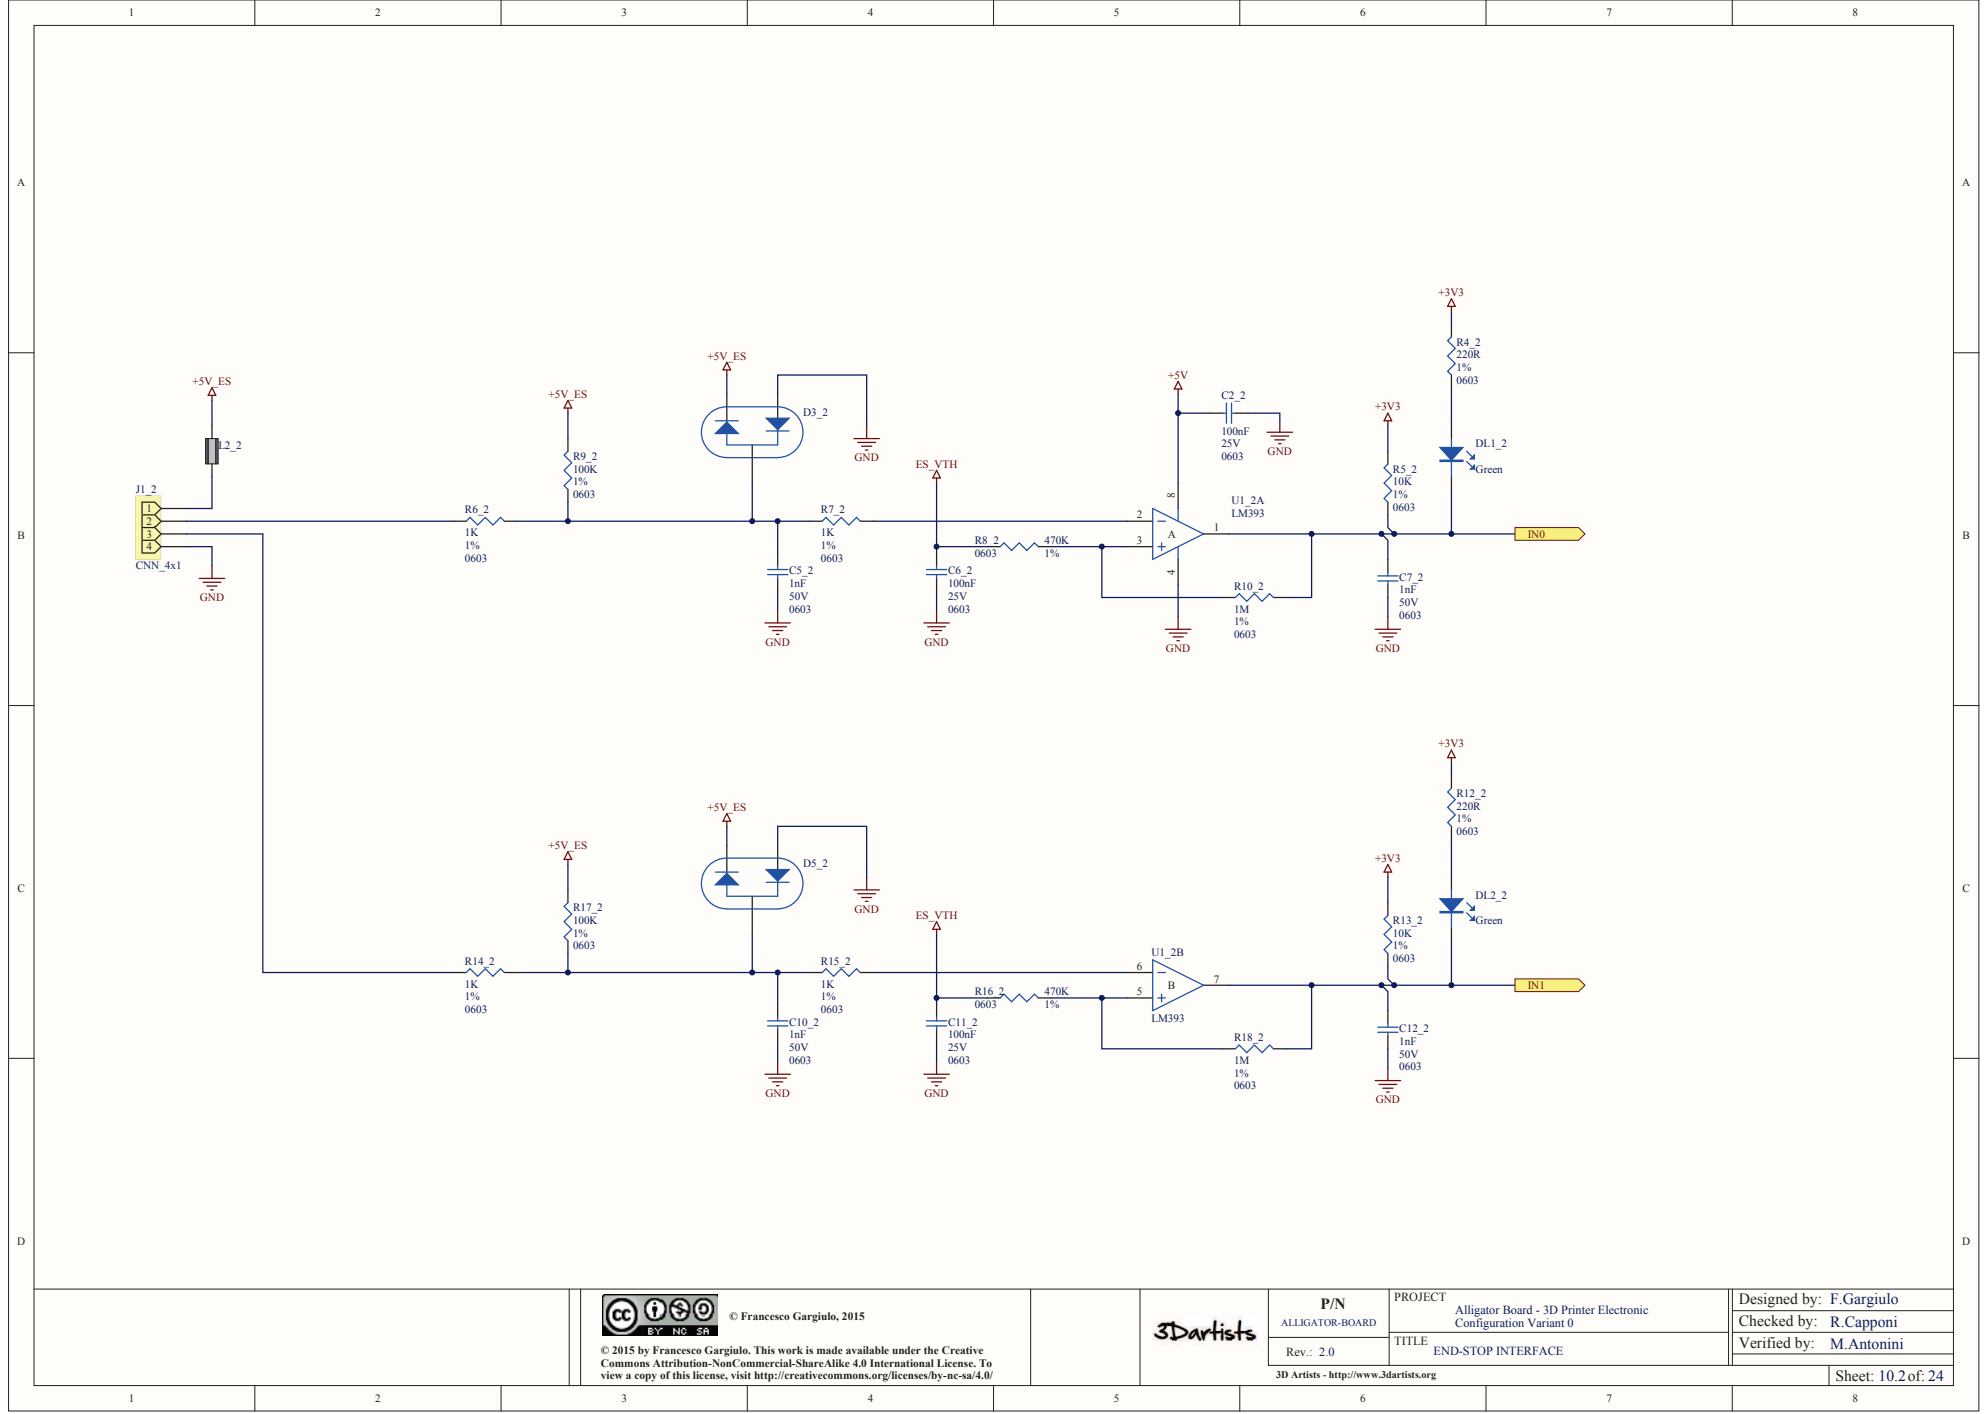
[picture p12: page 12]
GND; ES_VTH; Green; CNN_4x1

END-STOP INTERFACE

GND; ES_VTH; Green; CNN_4x1

END-STOP INTERFACE


MOTOR_STEP MOTOR_DIR; MOTOR_nFAULT; MOTOR_VREF; +12V_MOT; DNF 1%; MOTOR_nRESET; MOTOR_MODE_SEL; VMA; GND; VMB; VCP; nENBL 21 nSLEEP 17; DECAY 19; STEP 22 DIR 20 MODE0 24 MODE1 25 MODE2 26 nRESET 16; V3P3OUT 15; ISENA; ISENB; AOUT1; AOUT2; BOUT1; BOUT2; nHOME 27; AVREF 12; BVREF 13; nFAULT 18; DRV8825PWP; GND_IN

MOTOR DRIVER CHANNEL

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

MOTOR DRIVER CHANNEL

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

MOTOR DRIVER CHANNEL

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

MOTOR DRIVER CHANNEL

FAN OUTPUT; +12V_AUX; FAN_EN; GND_IN
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


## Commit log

2015-03-01 Schematic Files Updated
2015-03-01 Gerber Files Update
    [ALLIGATOR-BOARD-R01.GBL, ALLIGATOR-BOARD-R01.GBS, ALLIGATOR-BOARD-R01.GKO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]
2015-03-03 Schematic update.Component value and connection fix
    In the previous commit some components seem to have a wrong value, and
    some interconnections was incorrect. Some errors occured in the PDF
    generation process.
2015-04-01 Schematic Update
    updated schematic revision
2015-04-02 Assembly Documents added
    Assembly Drawings
    Part List
